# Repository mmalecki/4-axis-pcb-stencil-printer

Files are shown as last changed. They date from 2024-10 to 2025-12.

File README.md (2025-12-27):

# 4 Axis PCB Stencil Printer w/ Rotational Axis

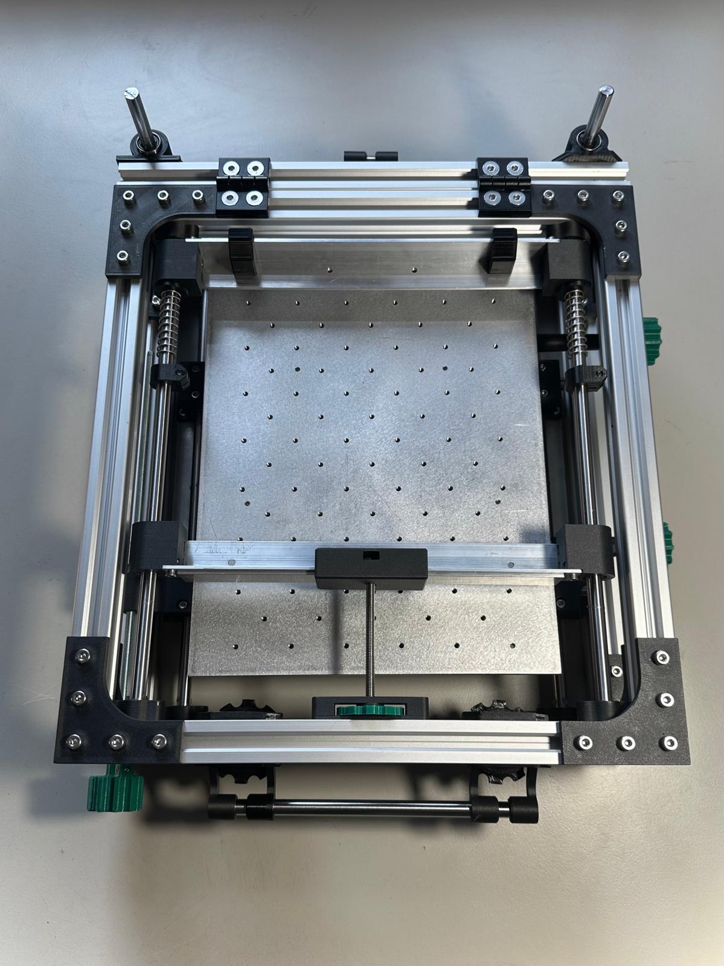
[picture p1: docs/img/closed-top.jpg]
Stencil printer shown from the top


This is a GitHub mirror/fork of the 4 Axis PCB Stencil Printer
with Rotational Axis by Philipp of [Dengler Mechatronik GmbH](https://dengler-mechatronik.de/).

You can find the source material on:
* [Thingiverse](https://www.thingiverse.com/thing:5690704)
* [Initial announcement](https://dengler-mechatronik.de/?p=560)
* [Digital build log](https://dengler-mechatronik.de/?p=790)

I chose to build this project because of its large working field,
and focus on what really matters - accurate stencil alignment.

All the modifications and their status is described below.

## Mods

### Top plate workholding
This mod adds workholding features (tapped holes) to the top plate,
making adding tooling a breaze.

Technical drawing: [`technical-drawings/top-plate-workholding.dxf`](`top-plate-workholding.dxf`)

Status: in use

### Linear Z axis
Caveat emptor: I never did manage to get the back of the eccenter Z axis working to my satisfaction.
The clamp either captured the threaded rod fully or not at all, not allowing for movement, or rendering
it in raspy freefall over the threads. It is possible I just didn't get it.

What I did manage to get working, however, is a Dremel against a left-over linear rod from a 3D printer,
and hence, the linear Z axis mod was born. It does away with the 2 x 140 mm long M8 threaded rods, and
replaces them with 2 x 140 mm long 8 mm linear rods riding on a bearing mounted to the top frame.
The eccenter mechanism is replaced with the same eccenter used on the front. In order to do that, the 2040
300 mm extrusion is swapped with a 2020 size extrusion of the same length.

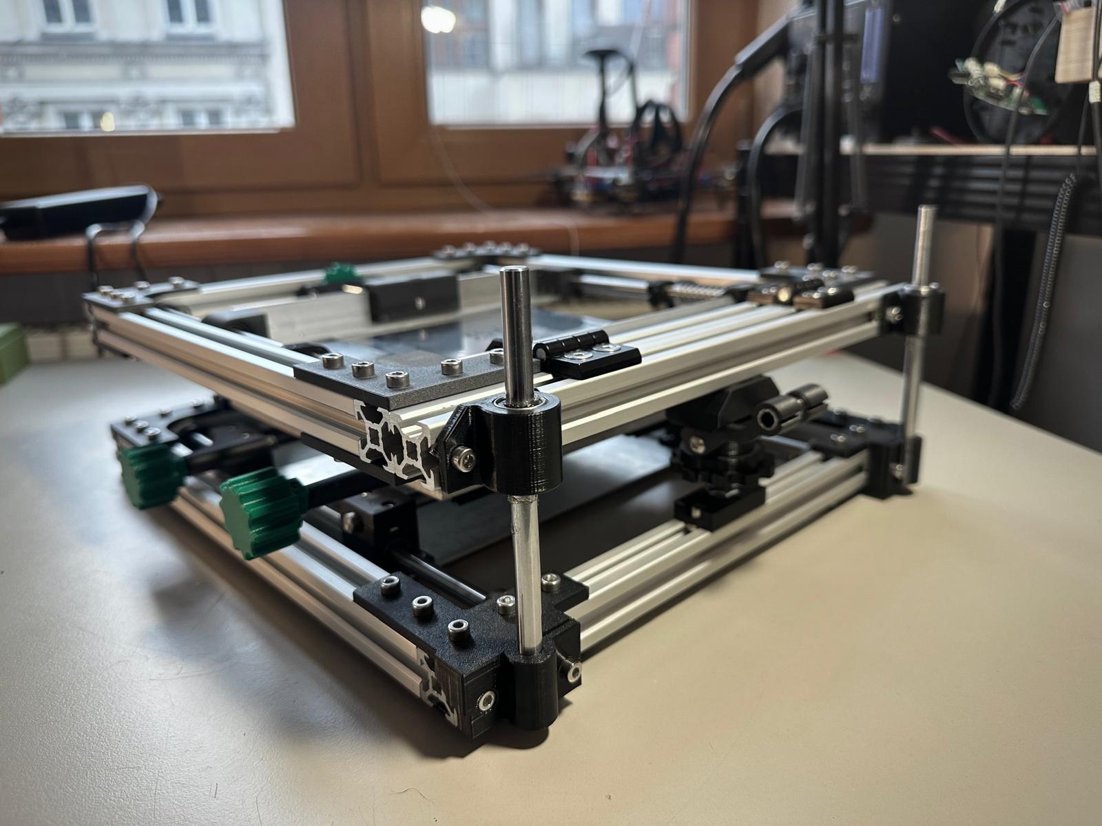
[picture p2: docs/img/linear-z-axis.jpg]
Linear Z axis modification, showing linear rods and their mounting


Status: in use

### Hinge locks
The hinges I used still allowed for some play between the back of the frame and the moving part.
Hence the hinge locks were born: if you're looking for repeatability across multiple applies,
or just to increase overall rigidity of the top frame when closed, this is the drop-in addon to print. 

Status: in use

### Bottom plate access holes
This mod replicates the 10 mm access hole seen in the bottom plate in all of five bolt locations.
It allows for easier maintenance and mounting of the threaded rod driven axis as a whole.

Status: in use

## Structure

* [`technical-drawings/`](technical-drawings/) - technical drawings in DXF and PDF formats for CNC manufacturing
* [`cad/`](cad/) - source CAD files, either original author's (STLs), or mine (FreeCAD, CadQuery)
* [`docs/`](docs/) - documentation

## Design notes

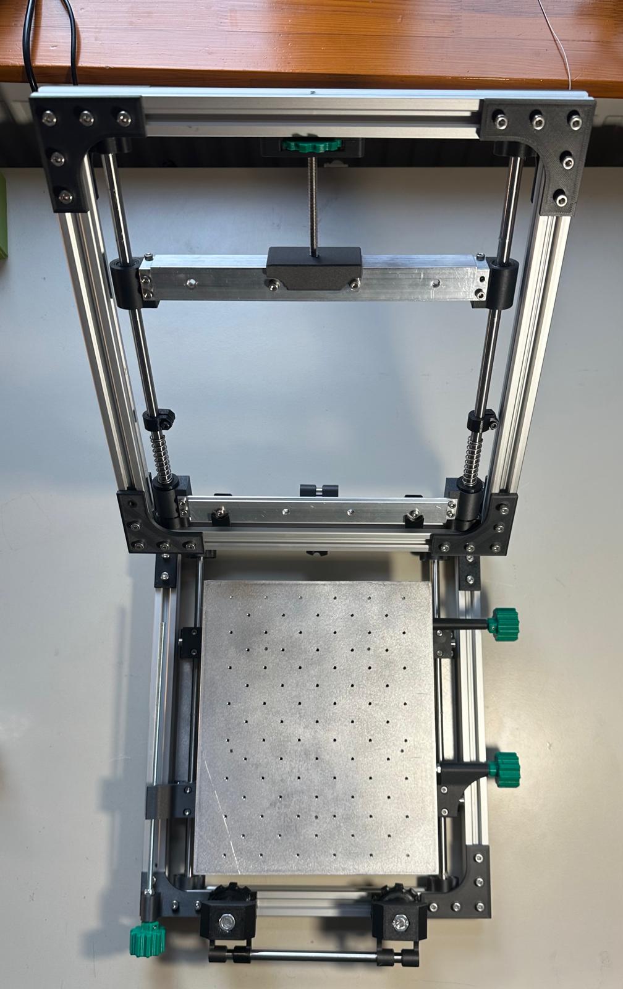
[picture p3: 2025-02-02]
docs/img/open-top.jpg

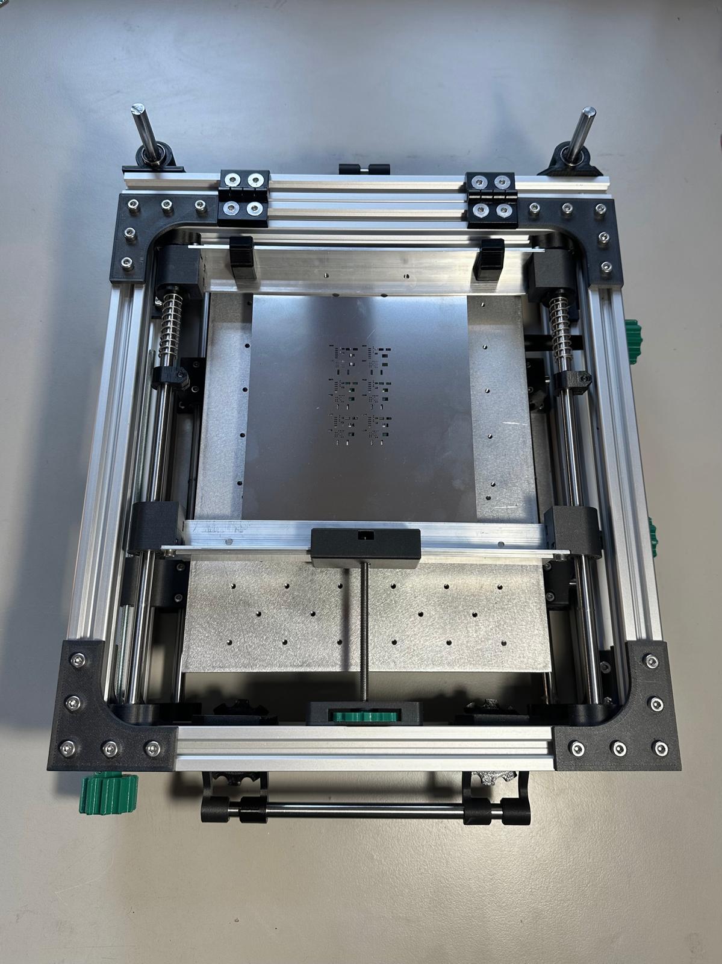
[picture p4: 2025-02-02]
docs/img/closed-top-stencil.jpg

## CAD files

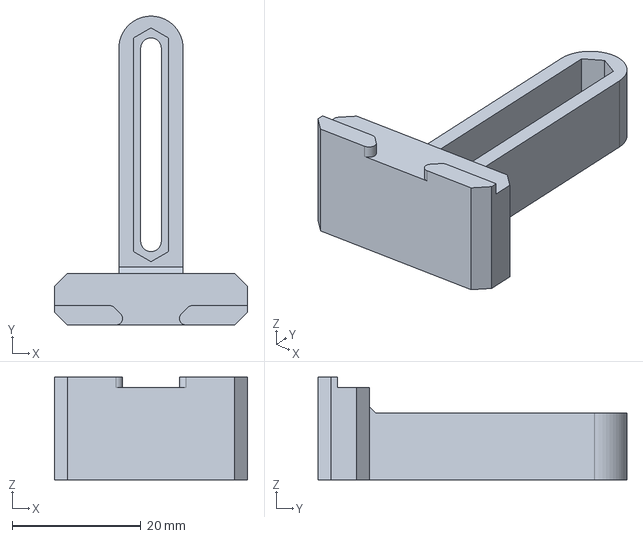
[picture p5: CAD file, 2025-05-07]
cad/board-mount/board-mount-static.FCStd
30.0 x 48.0 x 16.0 mm

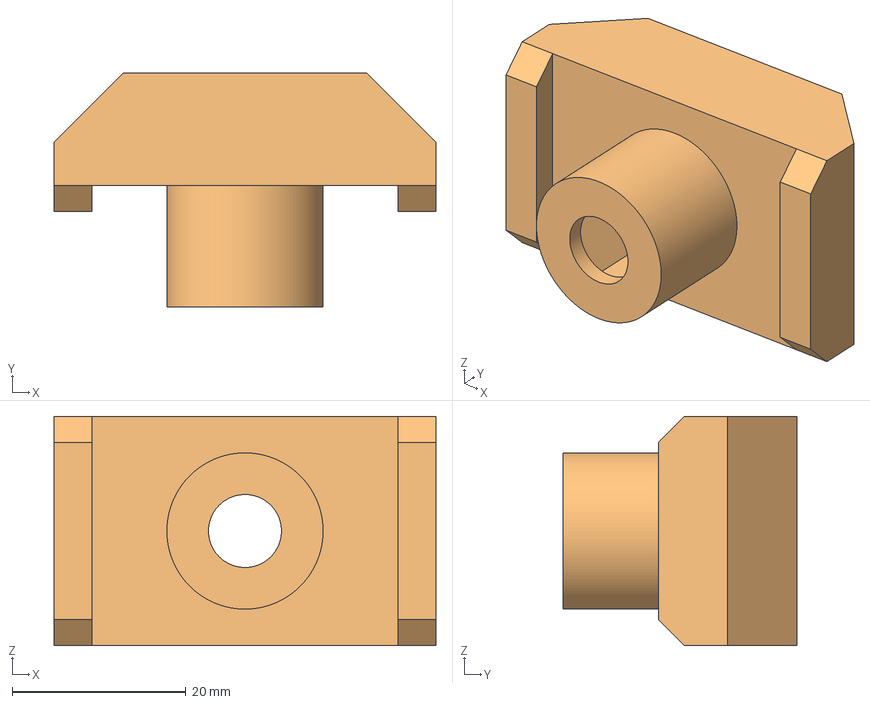
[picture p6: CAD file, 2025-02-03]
cad/ECCF_TOP.FCStd
44.0 x 27.0 x 26.4 mm
ECCF_TOP002
ECCF_TOP002 (Solid)
ECCF_TOP

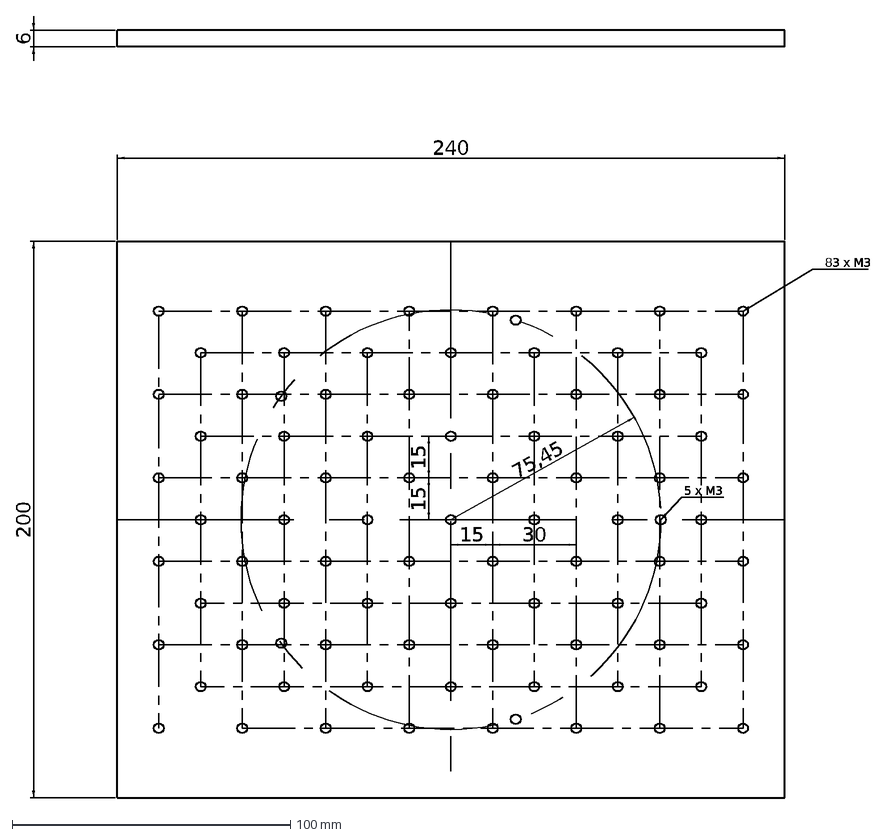
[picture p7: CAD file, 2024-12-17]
technical-drawings/top-plate-workholding.dxf
200
240
15
75,45
30
5 x M3
83 x M3
6

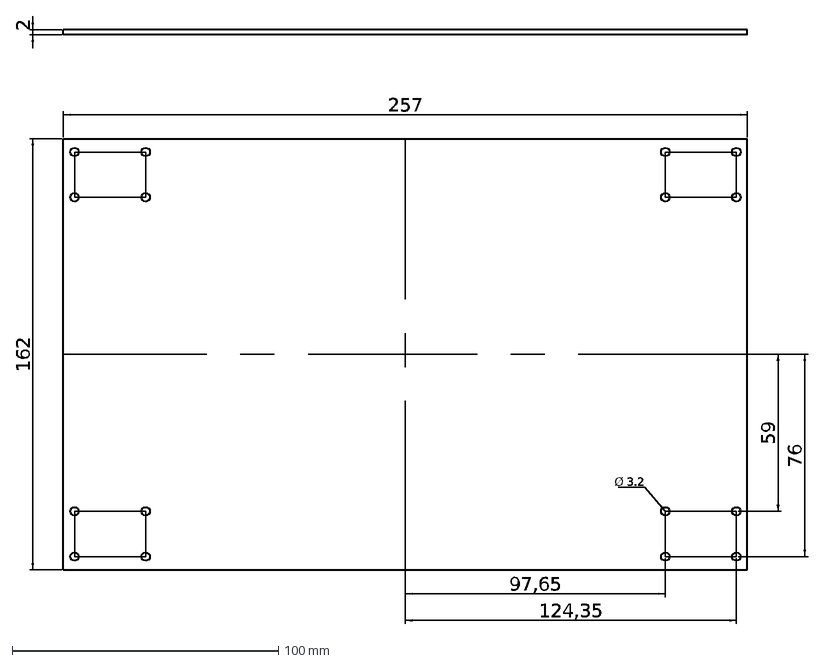
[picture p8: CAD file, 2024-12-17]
technical-drawings/base-plate.dxf
162
257
Ø 3.2
97,65
124,35
59
76
2

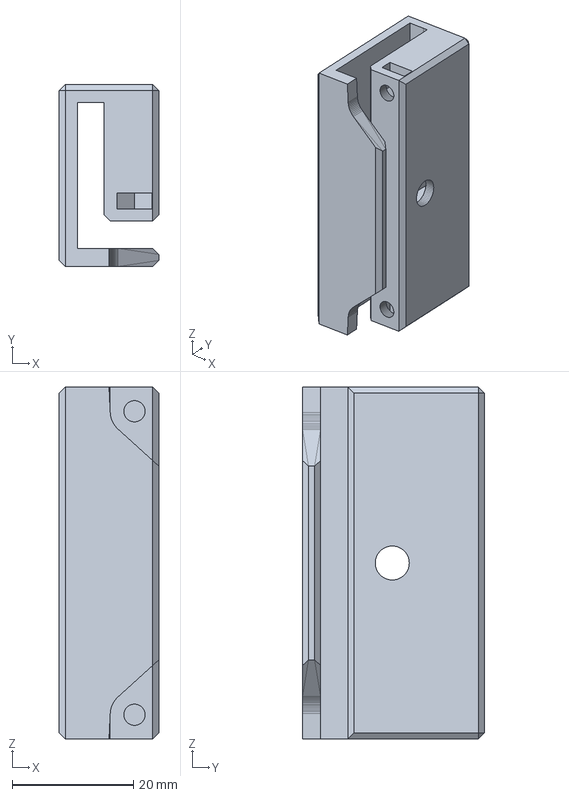
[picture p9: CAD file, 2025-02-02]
cad/TOP_CLAMP_SPANNER_COUNTER_4mm.FCStd
16.4 x 30.0 x 58.0 mm

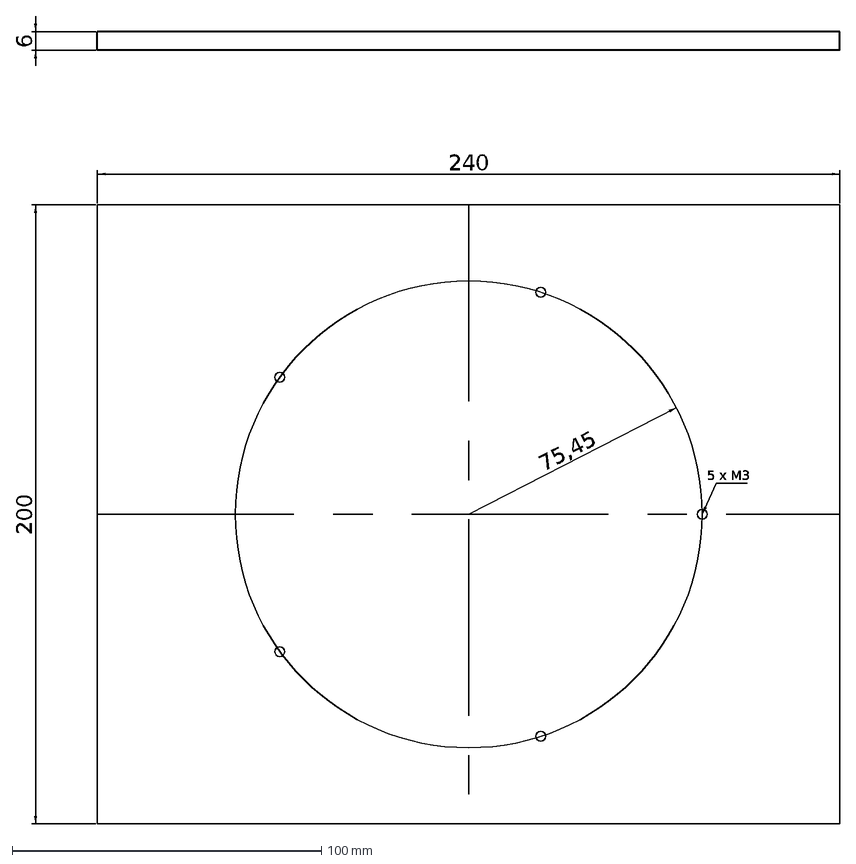
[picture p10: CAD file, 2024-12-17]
technical-drawings/top-plate-plain.dxf
200
240
75,45
5 x M3
6

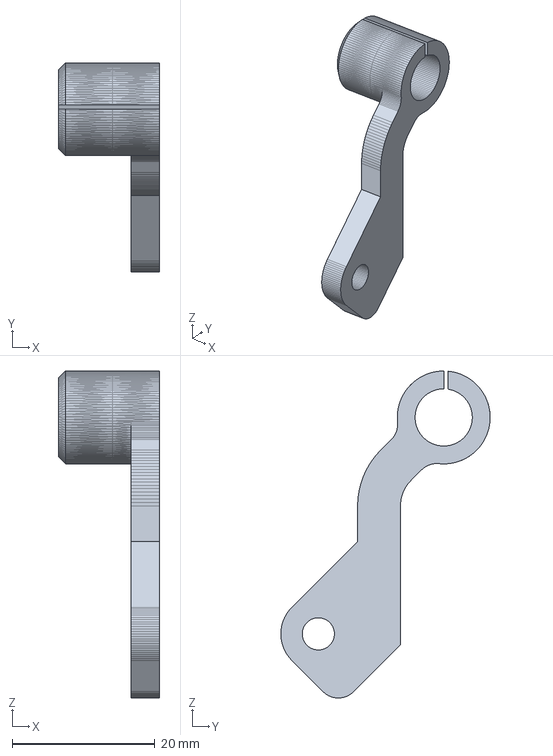
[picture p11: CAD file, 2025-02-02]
cad/ECCF_LEVER_COMPLIANT.FCStd
14.2 x 29.3 x 45.8 mm

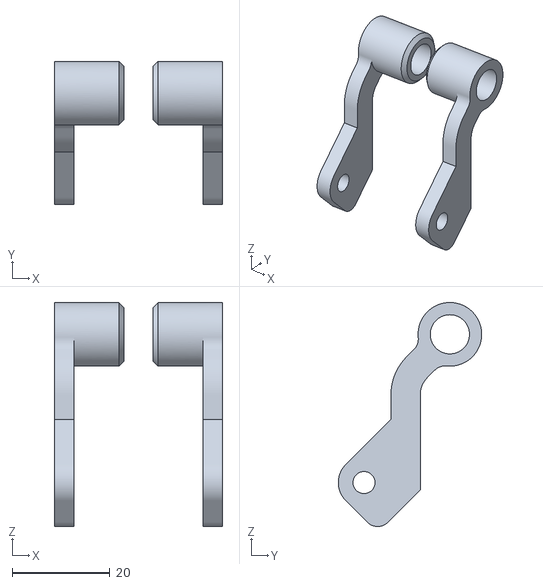
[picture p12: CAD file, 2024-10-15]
cad/ECCF_LEVER.stl
34.4 x 29.3 x 45.8

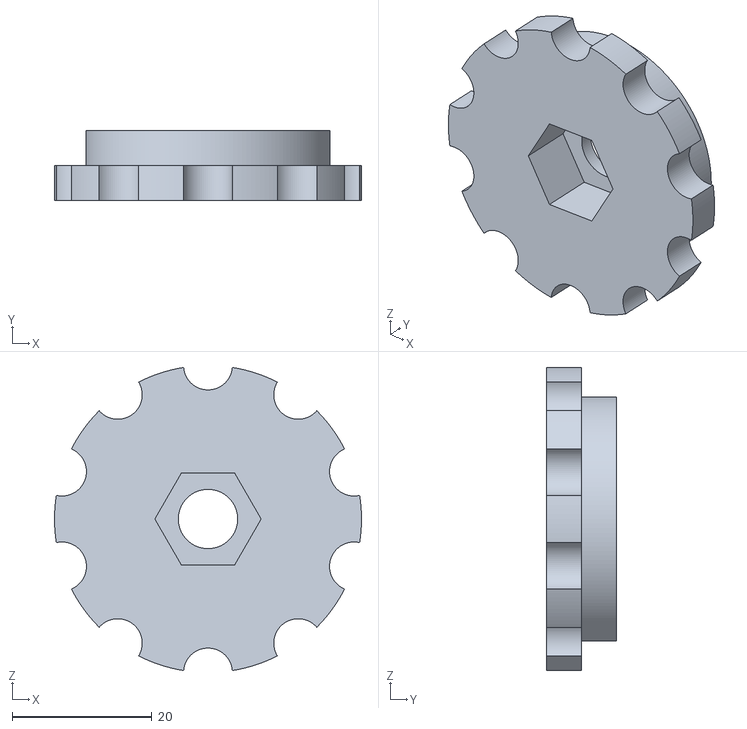
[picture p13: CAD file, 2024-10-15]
cad/ECCF_HEIGHT.stl
44.0 x 10.0 x 43.4

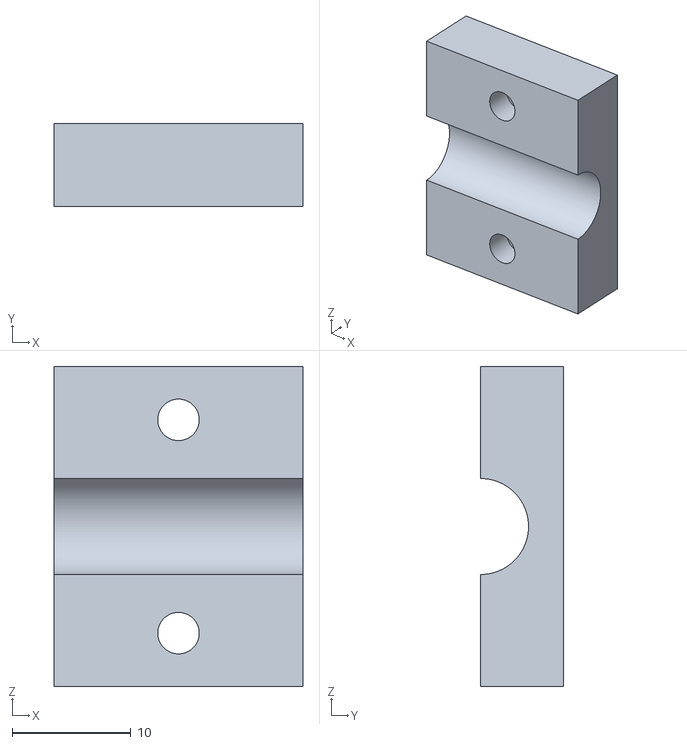
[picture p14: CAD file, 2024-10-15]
cad/BOT_RAIL_CLAMP_Y_AXIS.stl
21.0 x 7.00 x 27.0

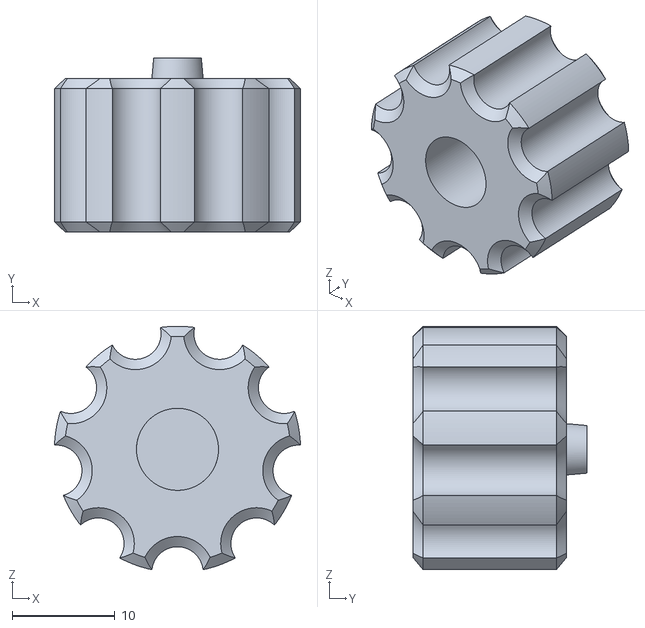
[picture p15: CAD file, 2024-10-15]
cad/BOT_Z_AXIS_COUNTER_KNOB.stl
24.0 x 17.0 x 23.7

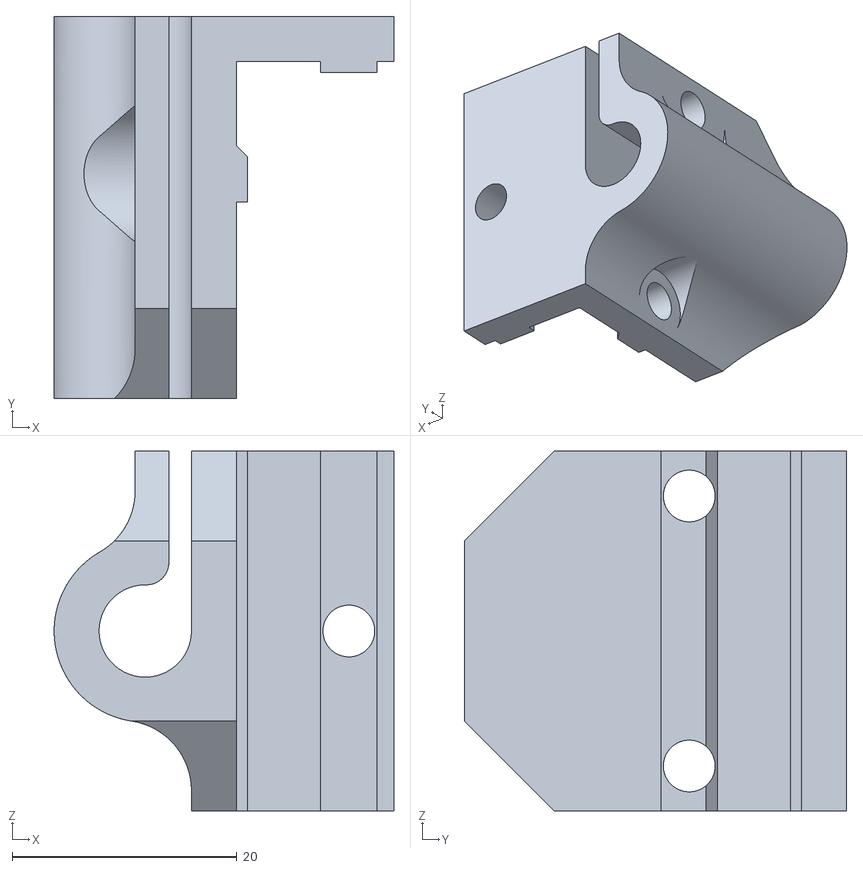
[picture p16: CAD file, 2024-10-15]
cad/TOP_CLAMP_Z_AXIS.stl
30.2 x 34.0 x 32.0

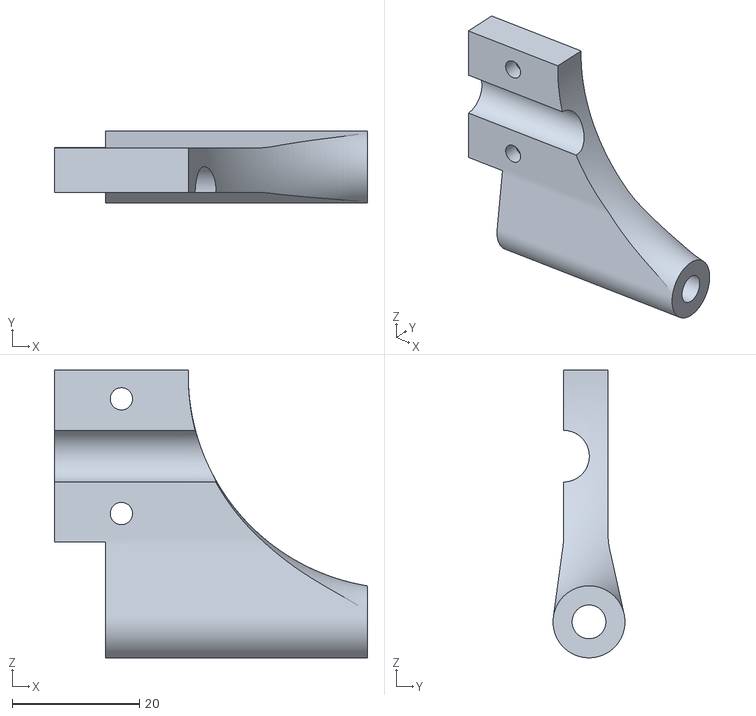
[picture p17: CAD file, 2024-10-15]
cad/BOT_RAIL_CLAMP_Y_AXIS_1.stl
49.1 x 11.3 x 45.1

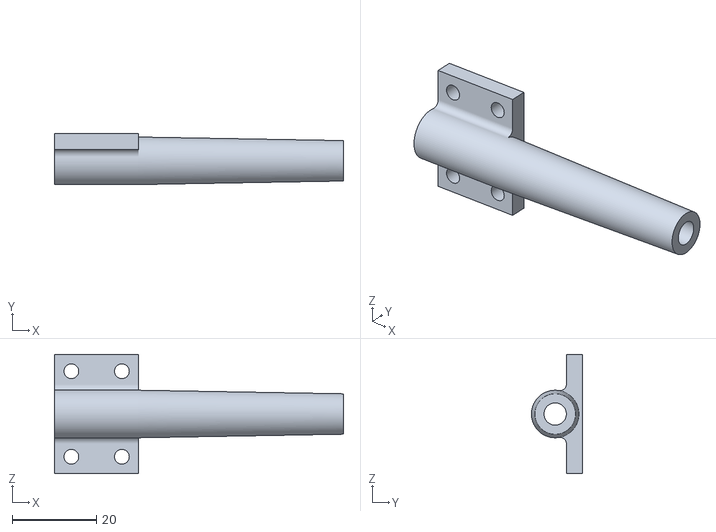
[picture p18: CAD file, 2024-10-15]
cad/BOT_ROD_HOLDER_ALPHA_AXIS.stl
68.6 x 12.2 x 28.3

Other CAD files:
cad/BOT_ROD_HOLDER_ALPHA_AXIS_SHORT.stl
cad/ADAPTER_D5_TO_M3.stl
cad/ECCF_BOT.stl
cad/TOP_CLAMP_SPANNER_COUNTER.stl
cad/BOT_BEARING_MOUNT_X_AXIS.stl
cad/BOT_BEARING_MOUNT_Y_AXIS.stl
cad/BOT_BEARING_MOUNT_Y_AXIS_DRIVEN.stl
cad/BOT_BRACKETS.stl
cad/BOT_BRACKET_X_AXIS.stl
cad/BOT_CLAMP_Z_AXIS.stl
cad/BOT_HANDWHEEL.stl
cad/BOT_RAIL_CLAMP_X_DRIVE.stl
cad/BOT_RAIL_HOLDER.stl
cad/BOT_RIGHT_ANGLE_CON.stl
cad/BOT_Z_AXIS_COUNTER_HOLDER.stl
cad/ECCF_MOUNT.stl
cad/ECCF_TOP.stl
cad/SR_BEARING_PLATE.stl
cad/SR_INNER_RING.stl
cad/SR_OUTER_RING_W_GEAR.stl
cad/SR_WORM_GEAR.stl
cad/STAND.stl
cad/TOP_CLAMP_BEARING_MOUNT_1.stl
cad/TOP_CLAMP_BEARING_MOUNT_2.stl
cad/TOP_CLAMP_NUT_HOLDER.stl
cad/TOP_CLAMP_NUT_HOLDER_4mm.FCStd
cad/TOP_CLAMP_SPANNER_CASE_1.stl
cad/TOP_CLAMP_SPANNER_CASE_2.stl
cad/TOP_CLAMP_SPANNER_HANDWHEEL.stl
cad/TOP_CLAMP_STOP.stl
cad/TOP_HANDWHEEL_Z_AXIS.stl
cad/TOP_RAIL_HOLDER.stl
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

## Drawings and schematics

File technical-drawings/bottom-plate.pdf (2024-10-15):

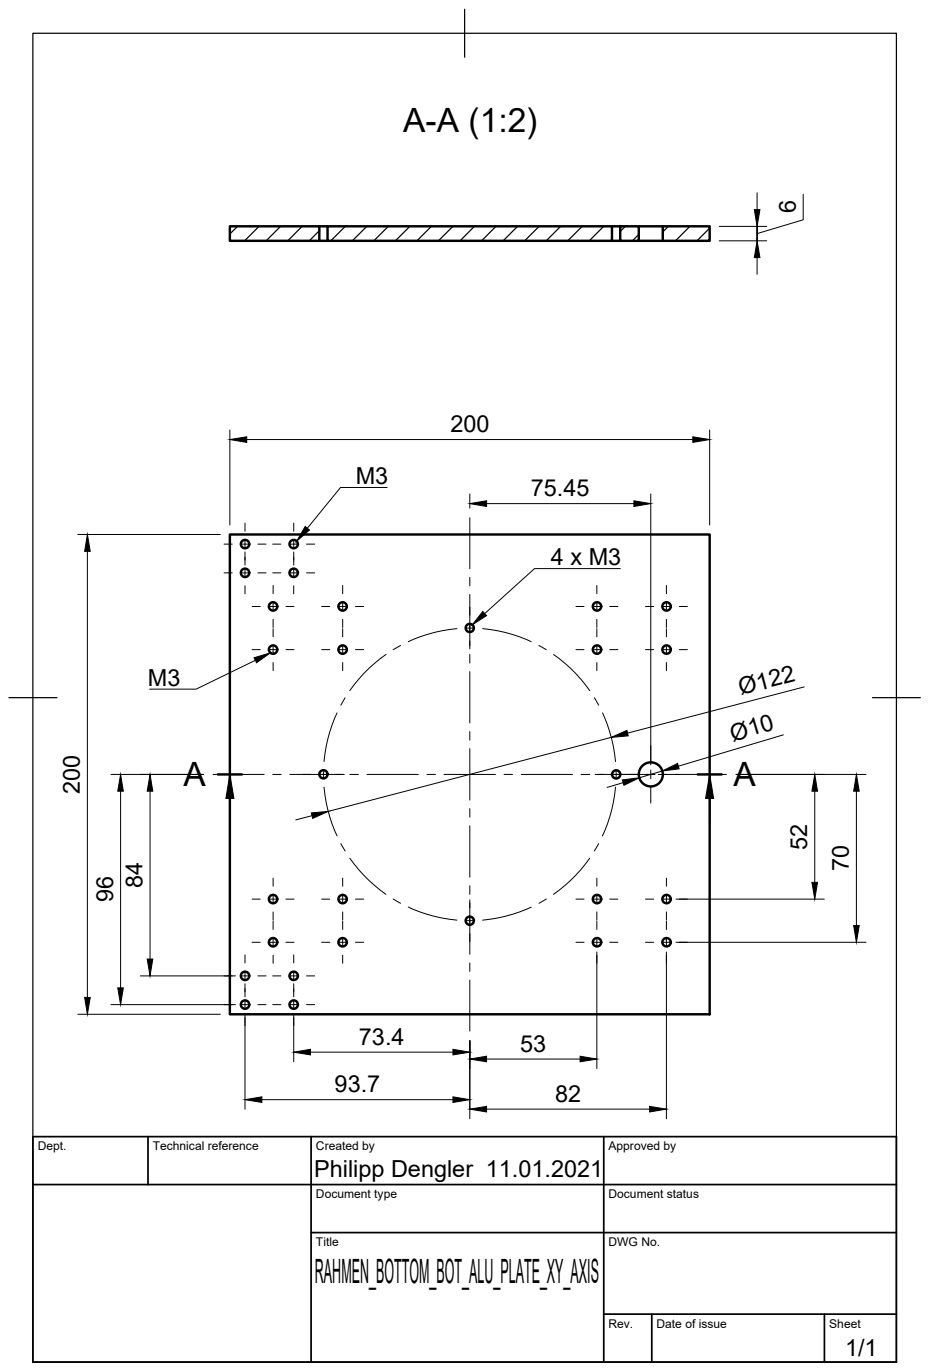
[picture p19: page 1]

Dept. | Technical reference | Created by Philipp Dengler 11.01.2021 | Approved by

Document type | Document status

Title RAHMEN_BOTTOM_BOT_ALU_PLATE_XY_AXIS | DWG No.

Rev. | Date of issue | Sheet 1/1

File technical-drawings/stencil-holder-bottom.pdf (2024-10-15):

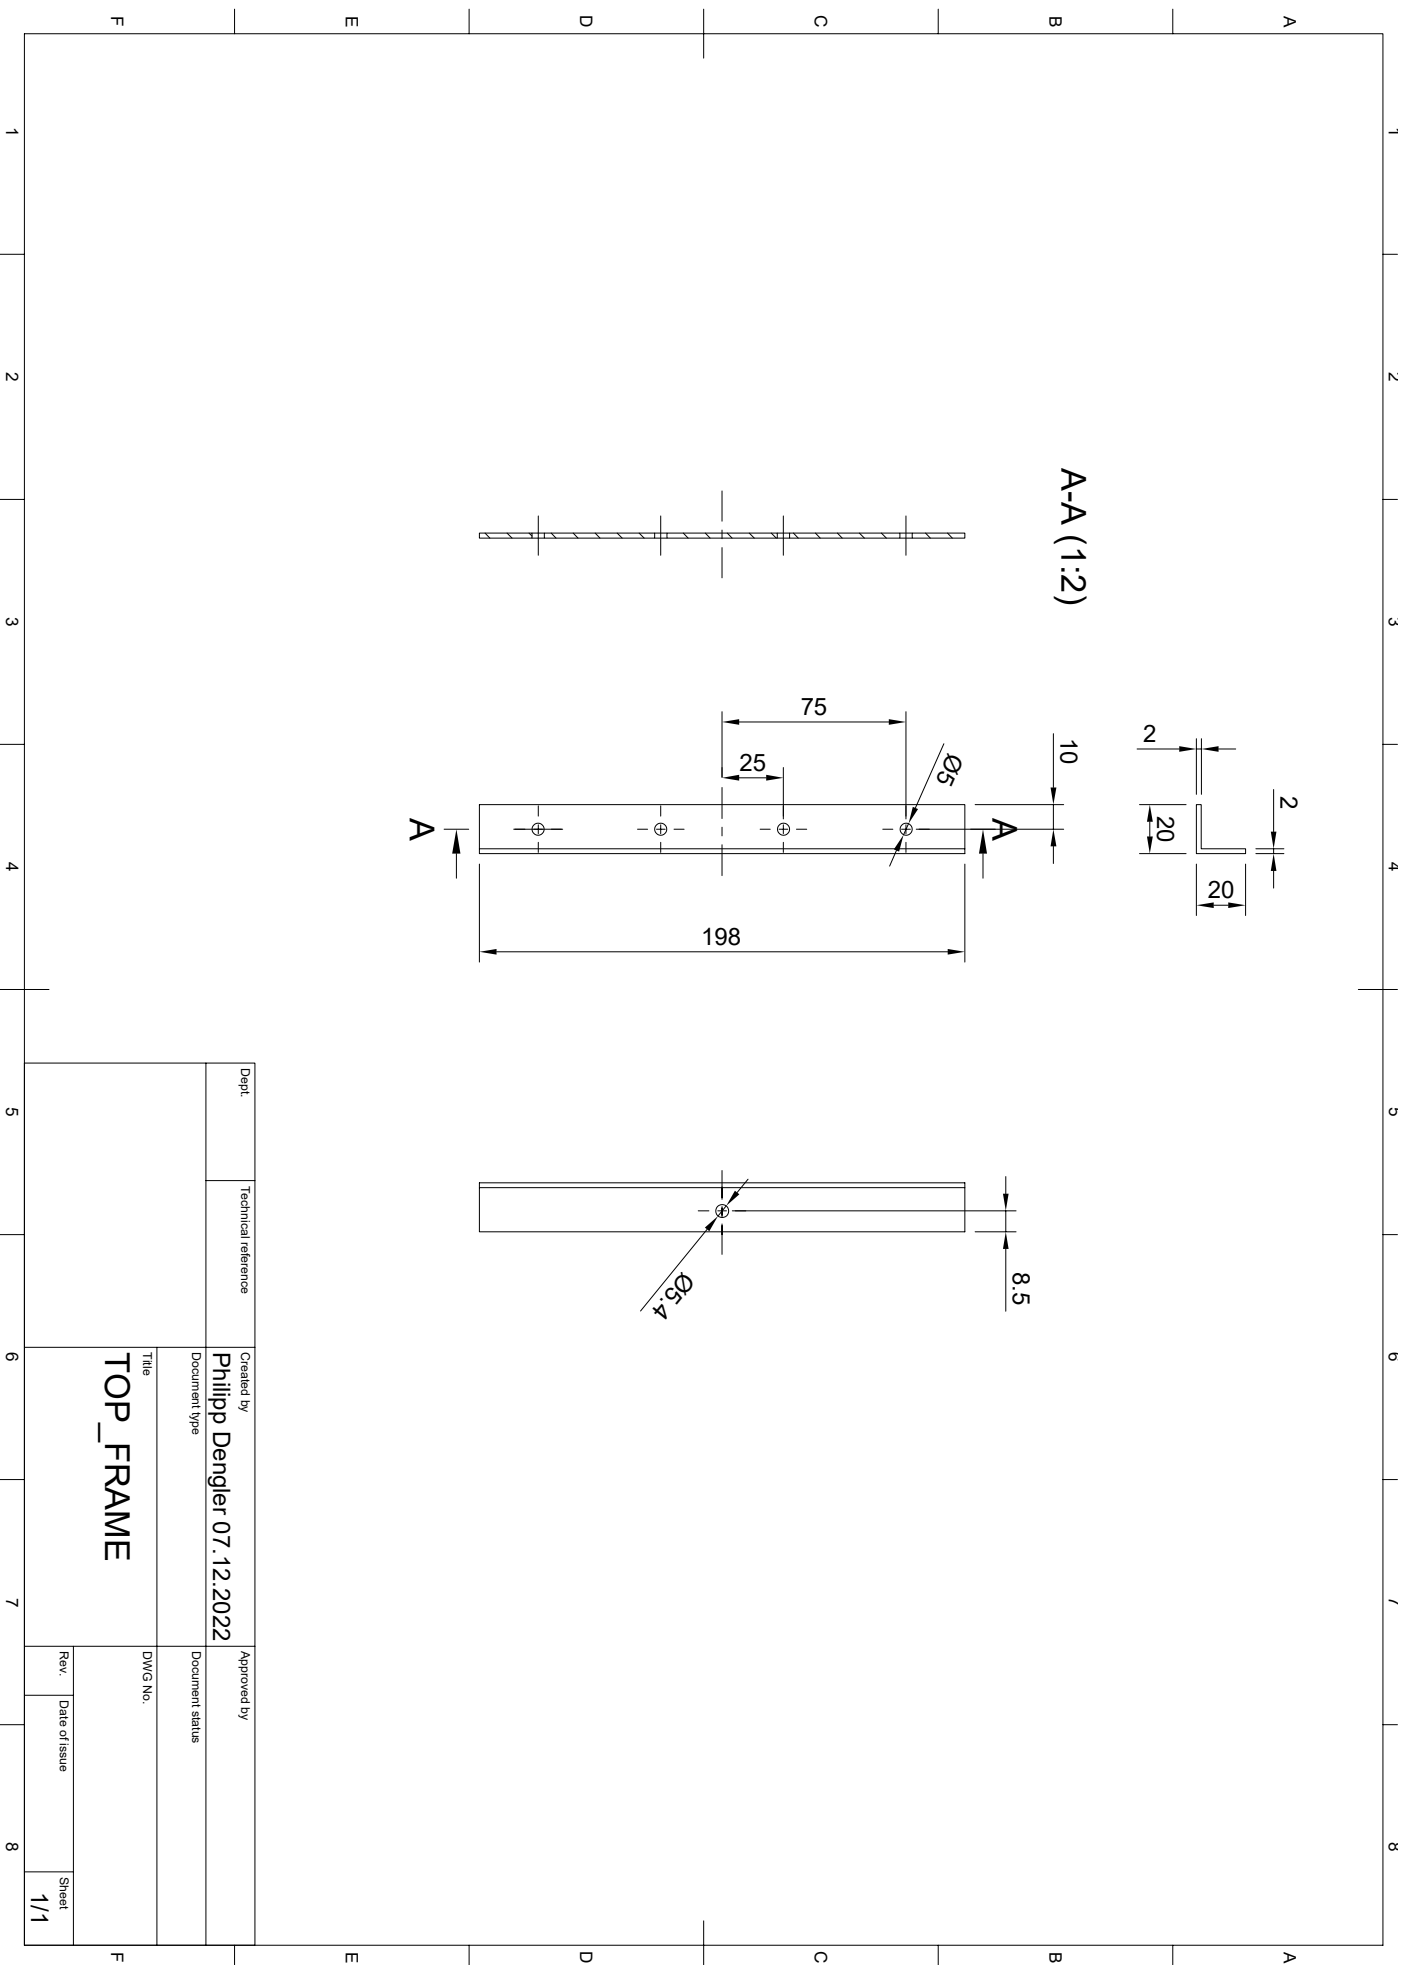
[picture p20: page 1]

1 A 2 3 4 5 6 7 8 1 2 3 4 5 6 7 8 FEDCB FEDCBA Dept. Technical reference Created by Approved by Title DWG No. Document type Document status Rev. Date of issue Sheet 07.12.2022 1/1 TOP_FRAME Philipp Dengler AA A-A (1:2)

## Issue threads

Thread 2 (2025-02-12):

Tensioning the rotary gear

mmalecki, 2025-02-12:
The gear could be pretensioned with... something, removing backlash. A screw would introduce friction, so maybe a ball on a magnet? A captive roller bearing?

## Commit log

2024-10-15 Add the existing CAD files
    [ADAPTER_D5_TO_M3.stl, BOT_BEARING_MOUNT_X_AXIS.stl, BOT_BEARING_MOUNT_Y_AXIS.stl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]
2024-12-17 Add base plate and two top plate variants
    [base-plate.dxf, top-plate-plain.dxf, top-plate-workholding.dxf]
2025-01-31 Change how plate DXFs are exported
2025-02-02 Add new Z axis parts
    Tidy up `settings.py`.
2025-02-02 Add in compliant versions of the levers
    The fit on the original holder is rather unforgiving.
    [ECCB_LEVER_COMPLIANT.FCStd, ECCF_LEVER_COMPLIANT.FCStd]
2025-02-02 Describe the linear Z axis mode
2025-02-02 Add 4 mm versions of the stencil clamp parts
    [TOP_CLAMP_NUT_HOLDER_4mm.FCStd, TOP_CLAMP_SPANNER_COUNTER_4mm.FCStd]
2025-02-03 Remove no longer used back eccenter files
    [ECCB_BODY.stl, ECCB_LEVER.stl, ECCB_LEVER_COMPLIANT.FCStd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]
2025-02-03 Add a ECCF_TOP FreeCAD import
    [ECCF_TOP.FCStd]
2025-02-19 Add hinge locks
2025-05-07 Add a static board mount stolen from LumenPnP
    [board-mount-static.FCStd]
2025-05-11 Add initial implementation of the microscope mount
2025-05-14 Add a board support
2025-07-20 Finish the microscope mount and LED mounts
2025-12-27 Add a CAD implementation of the bottom plate
    Add access holes and a central hole to the bottom plate.
2025-12-27 Use `ocp_vscode` in `top-plate.py`
2025-12-27 Document the bottom plate access holes mod
